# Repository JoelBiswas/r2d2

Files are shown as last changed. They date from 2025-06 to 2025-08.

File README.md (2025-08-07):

# R2-D2 - A Robotics Journey
The repository contains the files to build a smaller-scale replica of the R2-D2 droid from the Star Wars universe. The robot can move around and rotate its head, just like in the movies. It is controlled with a PS3 controller. This robotics project was created entirely by me for Hack Club's Highway to Undercity event.



FrontView

## Bill of Materials
View the Bill of Materials [here](https://docs.google.com/spreadsheets/d/11K8ikvZwUrrph38blHlkMEm7u3jJ6bzhOUvdLzmd2ws/edit?usp=sharing)

## The Start of the Journey
As a **HUGE** Star Wars fan and a robotics enthusiast, I have always thought it would be so cool to have my very own droid, just like the characters from the movies. Through my two years of experience in a FIRST Robotics Competition team (shoutout team 9477), I was able to learn all the skills I would need to build my own droid. When I was introduced to the Hack Club's Highway to Undercity event, which provides high school students with grants to build their dream projects, I knew that this would be the perfect opportunity for me to practice my robotics skills by building a droid. I decided to attempt to build R2-D2, the most iconic droid of the Star Wars Universe.

## About R2-D2
In the movies, R2 has a wide range of abilities such as movement, flight, tasers, a holographic projector, etc. For this project, I decided to focus on two key points of functionality for the droid: movement and head rotation. The robot has three "feet" -- one on the left, one on the right, and one in the center -- each containing a Pololu 12V Motor attached to a wheel. A PS3 controller is used to control the motors and move the droid. A stepper motor is used to control the rotation of R2-D2's head. An ESP32 is used in order to control all of the motor drivers.

## Overview of this Repo
**CAD** - Contains the CAD files for the robot, along with images taken in Onshape <br>
**STLs** - Contains files for each part that needs to be 3D printed <br>
**Print** - Contains the 3d print files for the Flashforge Adventurer 5M <br>
**Electrical** - Contains files from KiCAD for the robot's wiring schematics and custom symbols <br>
**Code** - Currently empty but will eventually contain the code for controlling the robot with a PS3 controller. <br>
**JOURNAL.md** - Contains an overview of exactly how I designed and built this robot <br>
**BOM.csv** - A bill of materials for the project in CSV format <br>

## Designing the Robot
Click [here](https://cad.onshape.com/documents/fbad7fda3dbb0b1c2d9d3e12/w/7637877b99adba1fcadbcc49/e/54e6ed0ce40017a6b8cdbd53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) to view the Onshape document for this project. 
The electronic design was done in KiCAD. 

CAD
Wiring

## General Steps for Assembly
1. Print all parts in the STLs folder of this repo. **IMPORTANT NOTE** Print out the BodyButtonFill.stl file six times and print Foot.stl and FootCover.stl three times.
2. Cut out a 5.8" x 6.3" sheet out of 1/8" polycarbonate.
3. Begin assembling the head by hot-gluing the blue pieces into the indents found in the dome.
4. Bolt the top part of the Lazy Susan Bearing to the bottom of the head using M4 bolts. Use the opening in the back of the head to insert the bolts.
5. Hot glue the blue body pieces into the indents found on the body.
6. Bolt the polycarbonate sheet inside the body using 4 M4 bolts.
7. Attach the stepper motor to the inside of the body, on the top face, using 4 M3 bolts.
8. Add the shaft hub to the shaft of the stepper motor.
9. Bolt the shaft hub onto the bottom of the head using 4 M4 bolts.
10. Bolt the bottom of the Lazy Susan Bearing to the top of the body using 4 M4 bolts.
11. Hot glue the blue leg pieces into the indents on the left and right legs.
12. Bolt the left and right legs into the sides of the body using 8 M4 bolts
13. Assemble each of the three feet by placing the 12V motor in the mounting area and placing the wheel on the motor. The wheel should be aligned with the cutout on the bottom of the foot.
14. Attach the left foot, right foot, and center foot to the droid using 2 M4 bolts for each foot.
15. Zip tie each electronic component (1 ESP32, 3 MD10Cs, 1 A4988, 1 12V to 5V Buck Converter, 1 3S LiPo Battery) to the polycarbonate plate using the zip tie mounts
16. Use the wiring schematic in the Electrical folder of this repo to wire the electrical components
17. Attach all the covers using M4 bolts

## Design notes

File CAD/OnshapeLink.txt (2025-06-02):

https://cad.onshape.com/documents/fbad7fda3dbb0b1c2d9d3e12/w/7637877b99adba1fcadbcc49/e/54e6ed0ce40017a6b8cdbd53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

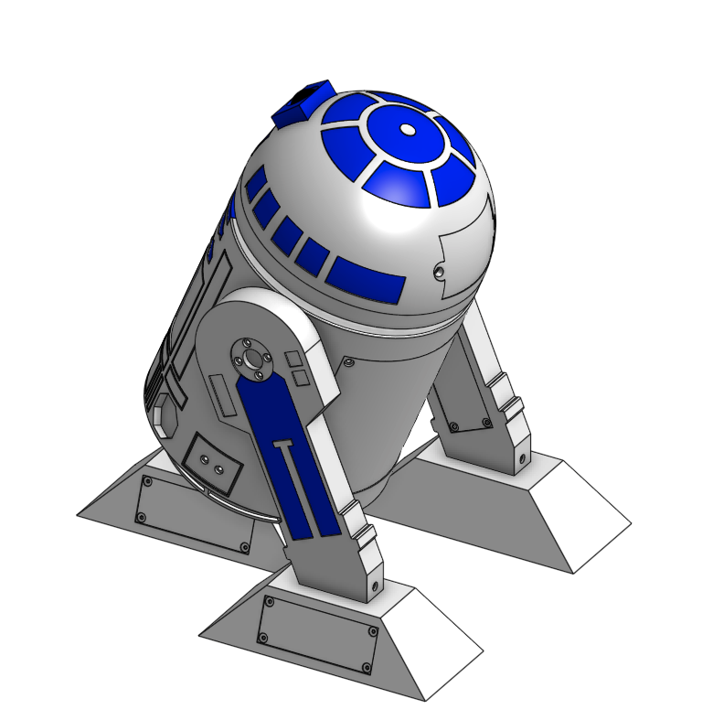
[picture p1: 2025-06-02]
CAD/Images/BackRightIsometric.png

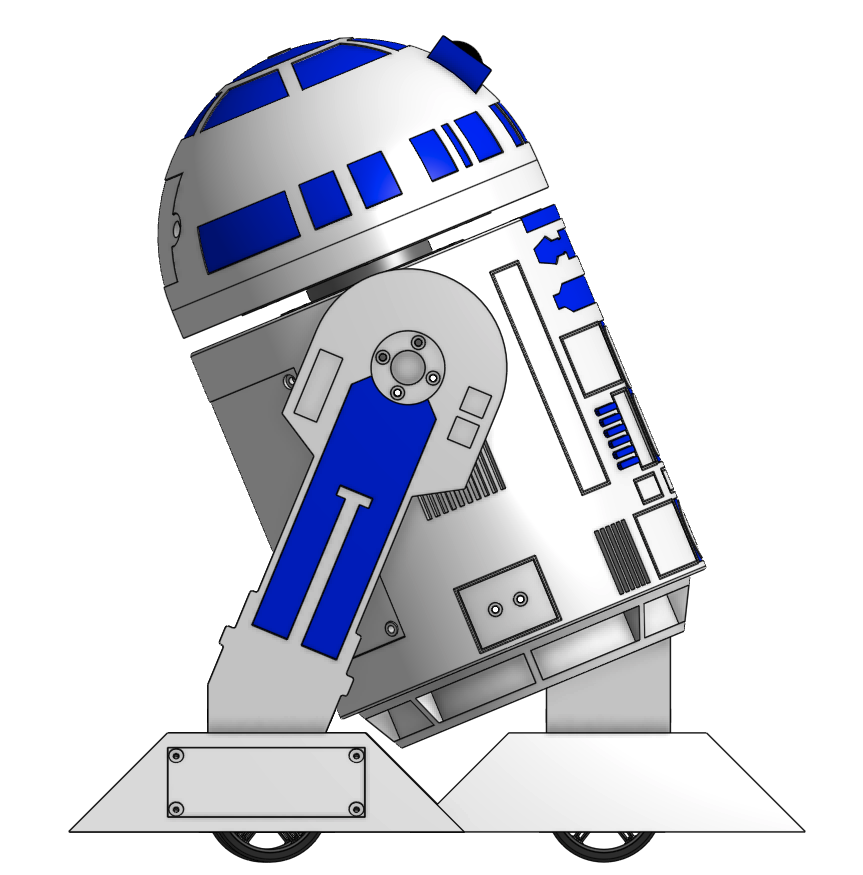
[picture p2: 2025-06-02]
CAD/Images/LeftView.png

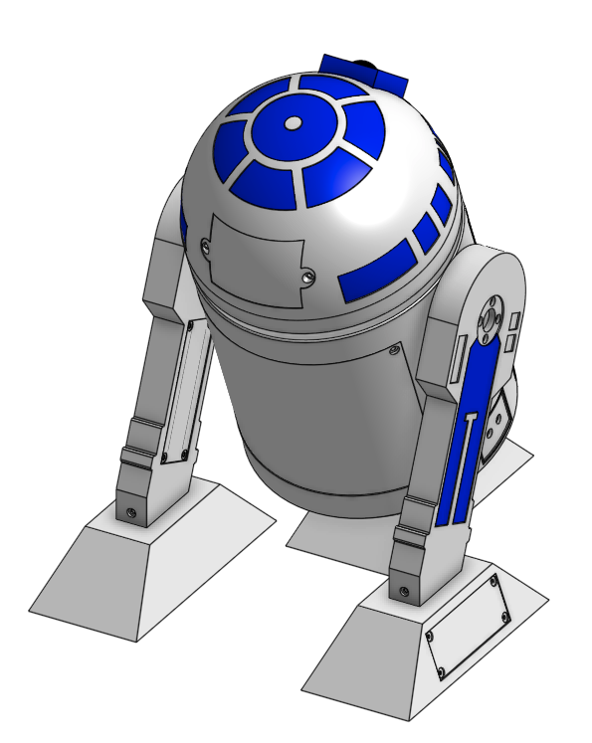
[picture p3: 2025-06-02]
CAD/Images/BackLeftIsometric.png

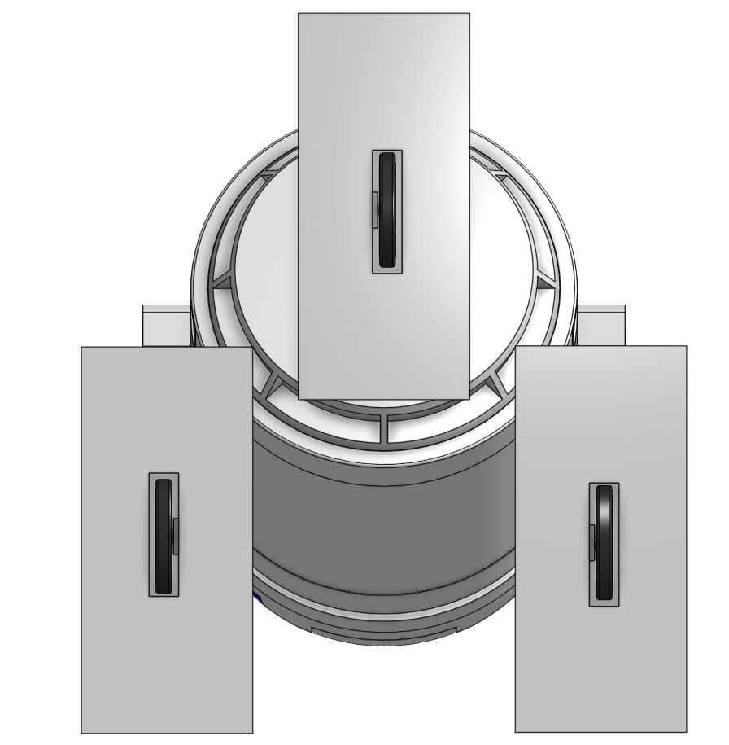
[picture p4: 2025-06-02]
CAD/Images/BottomView.png

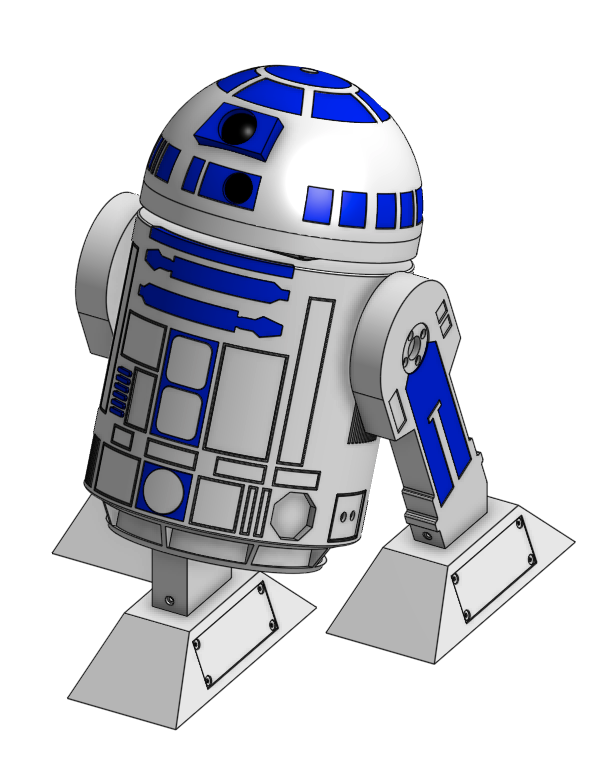
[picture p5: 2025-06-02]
CAD/Images/FrontRightIsometric.png

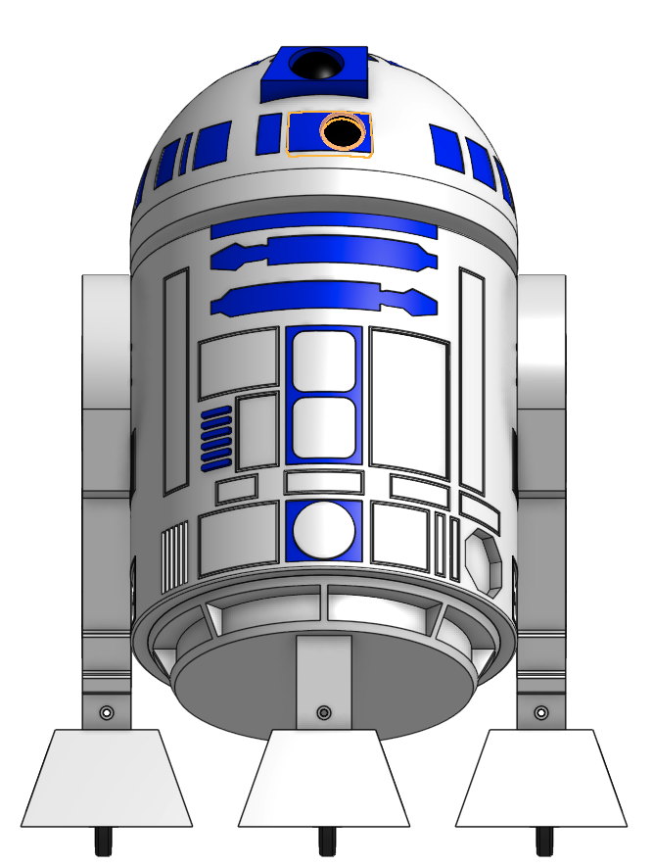
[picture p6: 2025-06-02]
CAD/Images/FrontView.png

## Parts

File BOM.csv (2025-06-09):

Part | Type | Quantity | Unit Price | Price | Link
Stepper Motor | Electrical Component | 1 | $14.00 | $14.00 | https://www.adafruit.com/product/324?gQT=1
Stepper Driver | Electrical Component | 1 | $9.95 | $9.95 | https://www.aliexpress.us/item/3256805909921734.html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:
DC Motor | Electrical Component | 3 | $22.45 | $67.35 | https://www.robotshop.com/products/12v-pololu-1501-micro-metal-gearmotor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
DC Motor Driver | Electrical Component | 3 | $13.90 | $41.70 | https://www.cytron.io/p-10amp-5v-30v-dc-motor-driver
ESP32 | Electrical Component | 1 | $4.31 | $4.31 | https://www.aliexpress.us/item/3256805517875317.html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:
3S LiPo Battery | Electrical Component | 1 | $12.89 | $12.89 | https://www.aliexpress.us/item/3256807696422912.html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:
LiPo Battery Charger | Electrical Component | 1 | $5.28 | $5.28 | https://www.aliexpress.us/item/3256807365682967.html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:
12V to 5V Buck Convertor | Electrical Component | 1 | $7.42 | $7.42 | https://www.aliexpress.us/item/3256808570929306.html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:
PS3 Controller | Electrical Component | 1 | $5.75 | $5.75 | https://www.aliexpress.us/item/2251832610701516.html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:
16 AWG Wire (Red + Black) (5m) | Electrical Component | 1 | $5.90 | $5.90 | https://www.aliexpress.us/item/3256807170658268.html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:
22 AWG WIre (Red + Black) (5m) | Electrical Component | 1 | $2.17 | $2.17 | https://www.aliexpress.us/item/3256807170658268.html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:
22 AWG Wire (White) (5m) | Electrical Component | 1 | $2.12 | $2.12 | https://www.aliexpress.us/item/3256801683674437.html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:
Wire Stripper | Electrical Component | 1 | $6.33 | $6.33 | https://www.aliexpress.us/item/3256807349448352.html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:
Electrical Tape | Electrical Component | 1 | $1.13 | $1.13 | https://www.aliexpress.us/item/3256805041931203.html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:
M4 Threaded Inserts (50 pack) | Fastener | 1 | $9.32 | $9.32 | https://www.mcmaster.com/94459A150
M3 Bolts (16mm) | Fastener | 1 | $2.05 | $2.05 | https://www.aliexpress.us/item/2251832255868282.html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:
M4 Bolts (50mm) | Fastener | 1 | $2.25 | $2.25 | https://www.aliexpress.us/item/2251832255868282.html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:
M4 Bolts (25mm) | Fastener | 2 | $1.49 | $2.98 | https://www.aliexpress.us/item/2251832255868282.html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:
Zip Ties (100 pack) | Fastener | 1 | $1.55 | $1.55 | https://www.aliexpress.us/item/3256805935303543.html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:
Zip Tie Mounts (50 pack) | Fastener | 1 | $1.69 | $1.69 | https://www.aliexpress.us/item/2255800615815847.html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:
Wheel (2-Pack) | Other | 2 | $8.75 | $17.50 | https://www.pololu.com/product/1430
Lazy Susan Bearing | Other | 1 | $6.99 | $6.99 | https://www.woodcraft.com/products/triangle-flat-square-lazy-susan-4-5-16-t-capacity-300-lbs
Shaft Hub | Other | 1 | $3.19 | $3.19 | https://www.robocore.net/item-mecanico/acoplador-5mm
1kg PLA Filament White | Other | 3 | $11.33 | $34.00 | https://www.amazon.com/ANYCUBIC-Filament-Printing-Dimensional-Accuracy/dp/B0DZ24ZZNR?sr=8-10
1kg PLA Filament Blue | Other | 1 | $17.99 | $17.99 | https://www.amazon.com/ANYCUBIC-Filament-Printing-Dimensional-Accuracy/dp/B0CZRK4Y52?sr=8-9
1/8" Thick Polycarbonate (12x12) | Other | 1 | $4.50 | $4.50 | https://www.amazon.com/LEXAN-POLYCARBONATE-CLEAR-THICK-PICK/dp/B074NB3XD1?gQT=0
Soldering Iron | Already Owned | 0 | $0.00 | $0.00
Solder | Already Owned | 0 | $0.00 | $0.00
Wire Cutters | Already Owned | 0 | $0.00 | $0.00
3D Printer | Already Owned | 0 | $0.00 | $0.00
Shipping + Tax Estimate | Other | 1 | $50.00 | $50.00
Total Price | $340.31

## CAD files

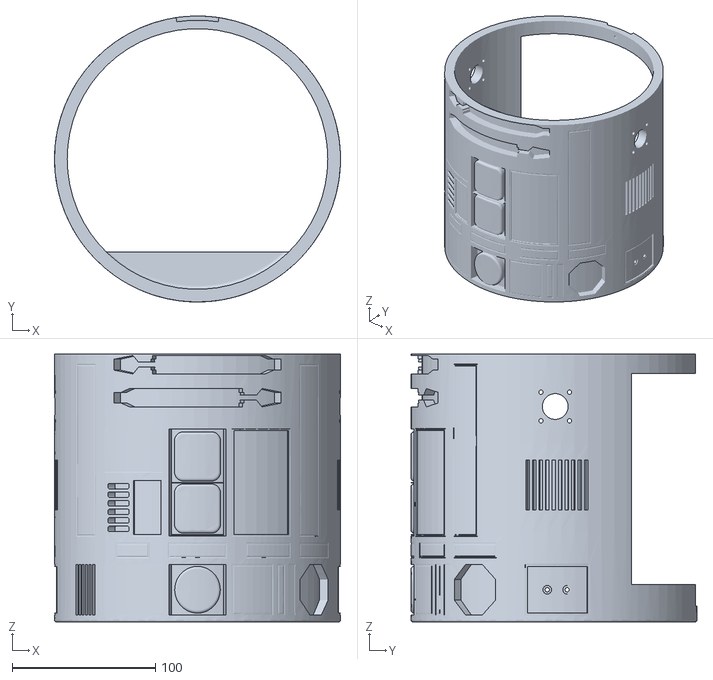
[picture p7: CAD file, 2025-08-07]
STLs/White/Body/BodyMain.stl
200.0 x 200.0 x 187.3

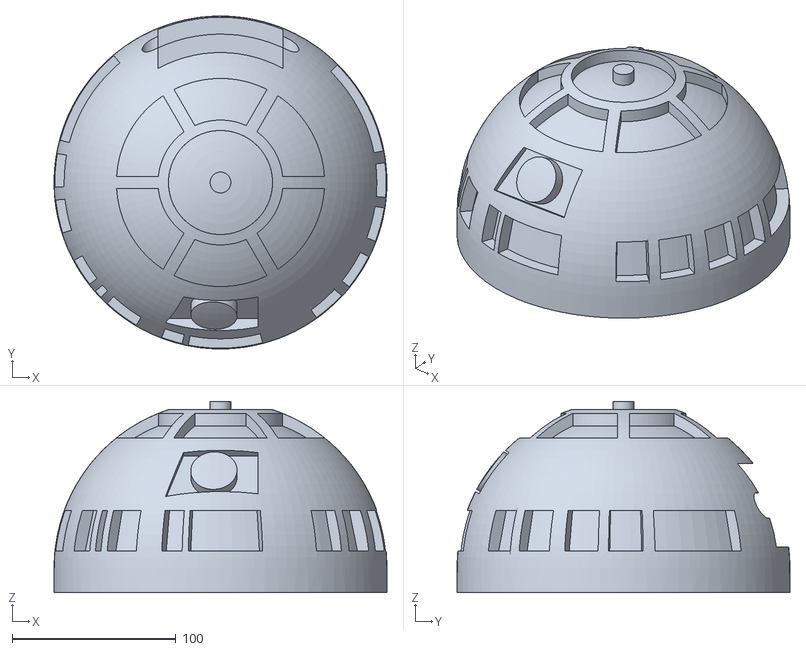
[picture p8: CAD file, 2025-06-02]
STLs/White/Head/HeadMain.stl
203.2 x 203.2 x 116.8

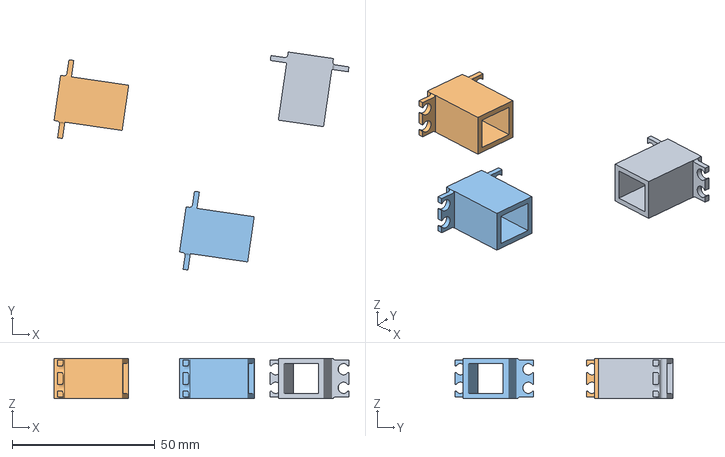
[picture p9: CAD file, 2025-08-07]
Print/Slicer/N20Case.3mf
103.2 x 76.3 x 14.0 mm
N20Case.stl x 3

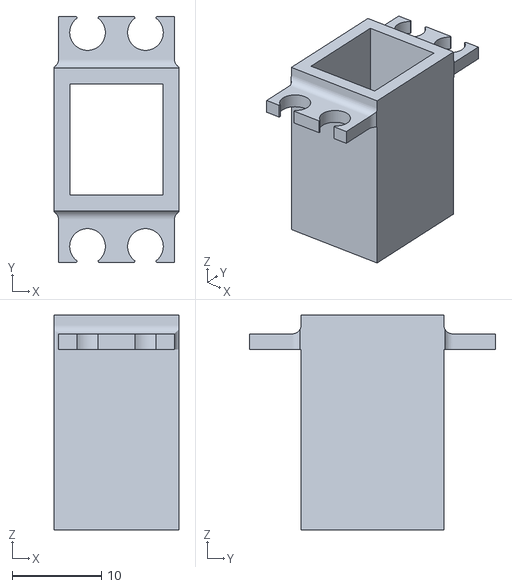
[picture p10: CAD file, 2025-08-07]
STLs/Black/Foot/N20Case.stl
14.0 x 27.6 x 24.1

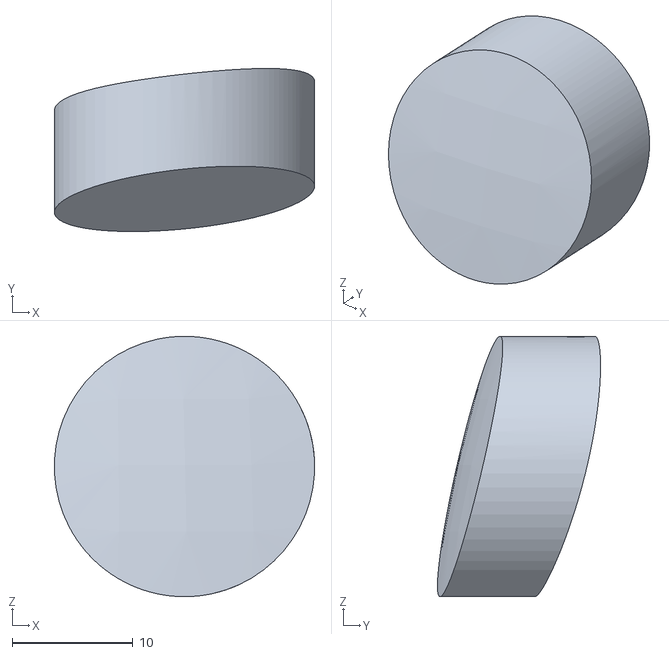
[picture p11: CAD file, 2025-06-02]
STLs/Black/Head/HeadStatusLight.stl
21.5 x 13.5 x 21.6

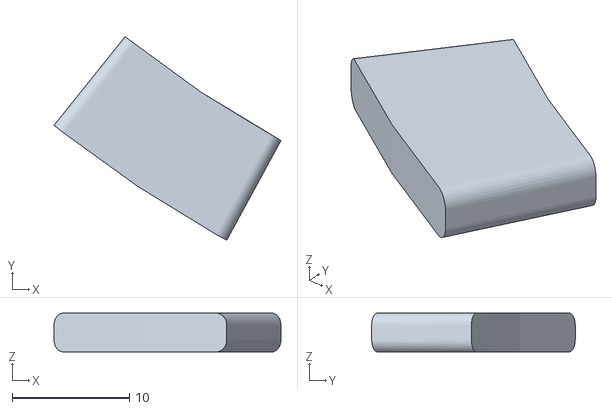
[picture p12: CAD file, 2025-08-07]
STLs/Blue/Body/BodyButtonFill2.stl
19.3 x 17.3 x 3.32

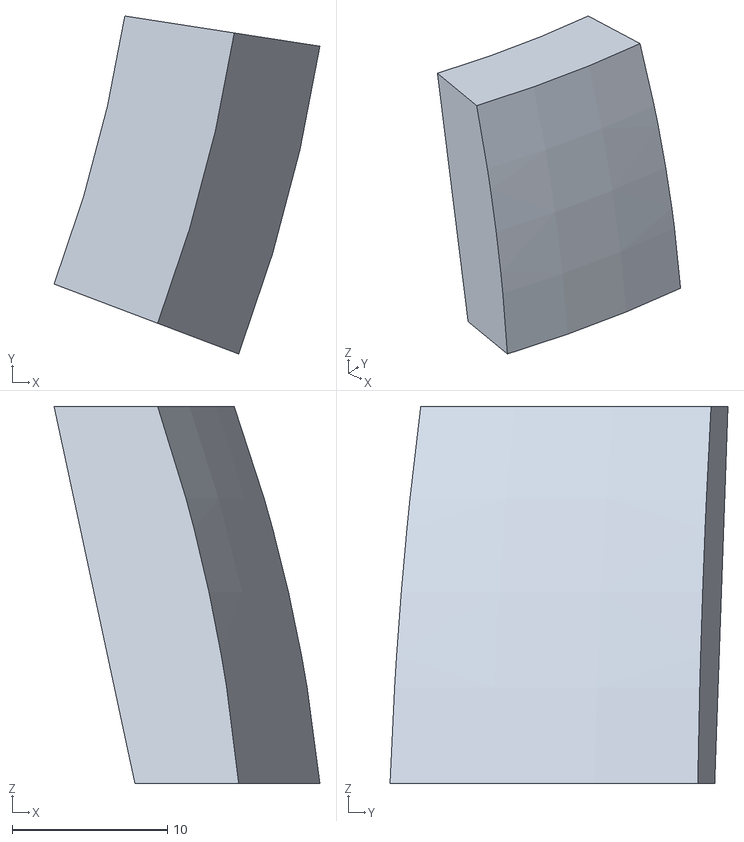
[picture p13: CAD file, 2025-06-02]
STLs/Blue/Head/HeadRightFill1.stl
17.1 x 21.7 x 24.2

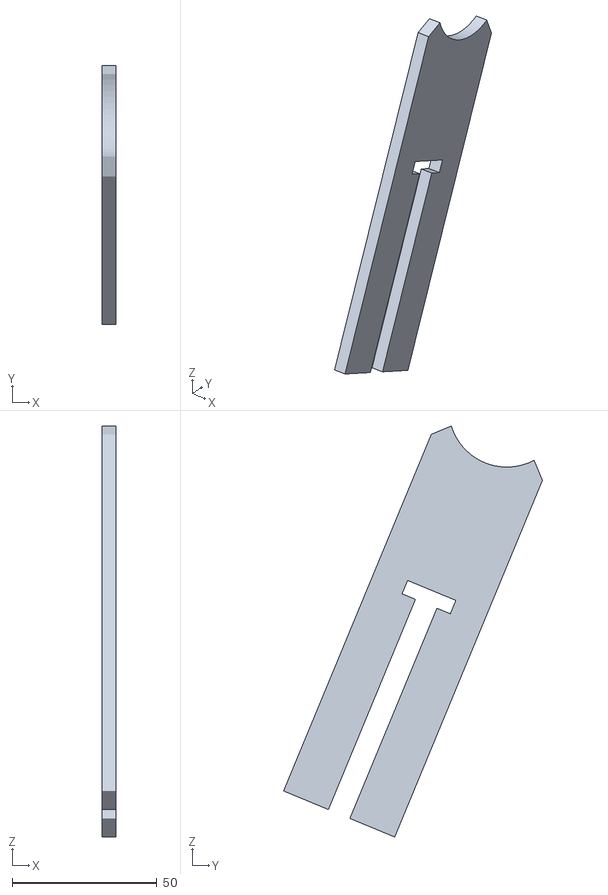
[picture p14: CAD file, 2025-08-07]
STLs/Blue/Leg/RightLegFill.stl
5.00 x 89.3 x 141.8

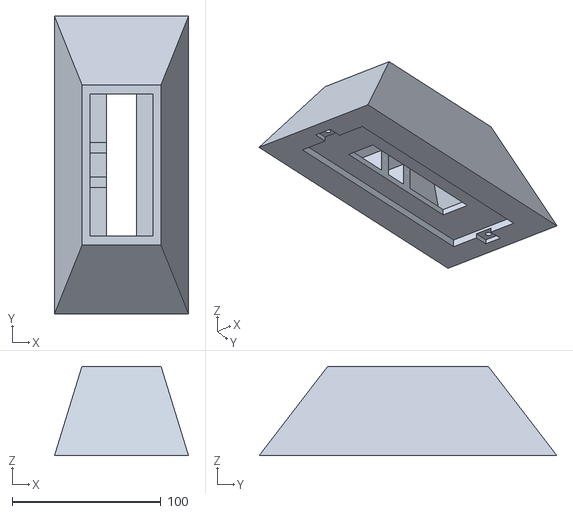
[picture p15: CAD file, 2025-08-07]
STLs/White/Foot/FootBottom.stl
90.0 x 200.0 x 60.0

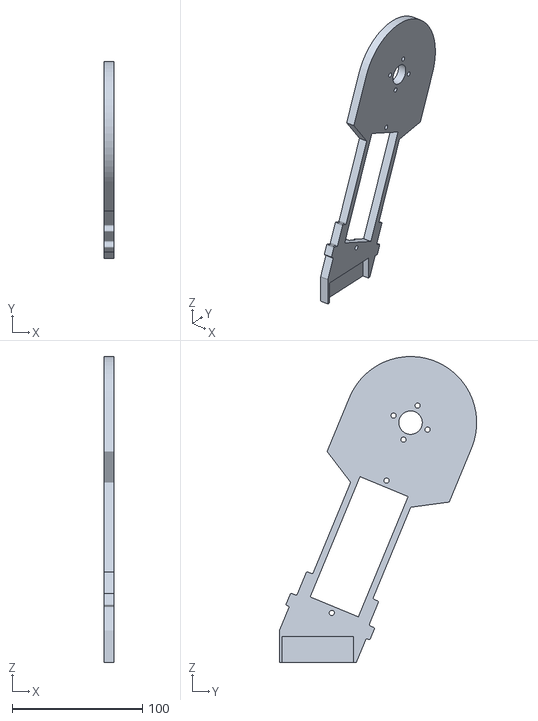
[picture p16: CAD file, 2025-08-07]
STLs/White/Leg/RightLegBottom.stl
8.00 x 151.6 x 235.1

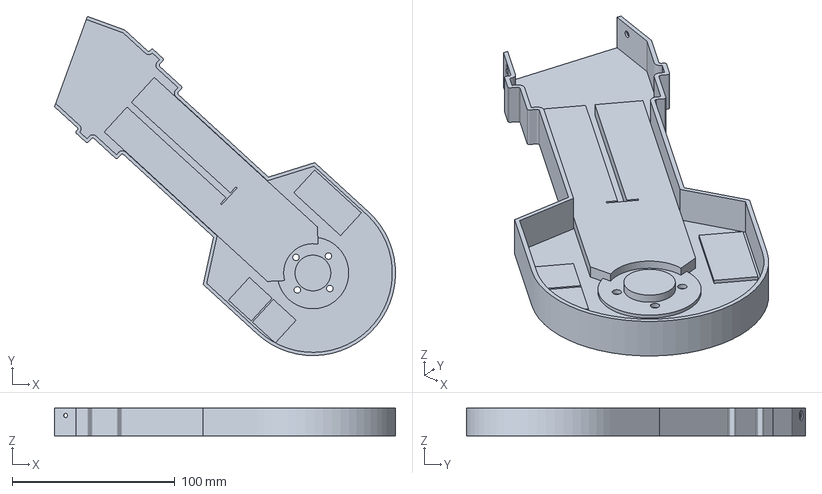
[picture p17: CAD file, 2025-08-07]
Print/Slicer/LeftLegTop.3mf
209.7 x 208.6 x 17.0 mm

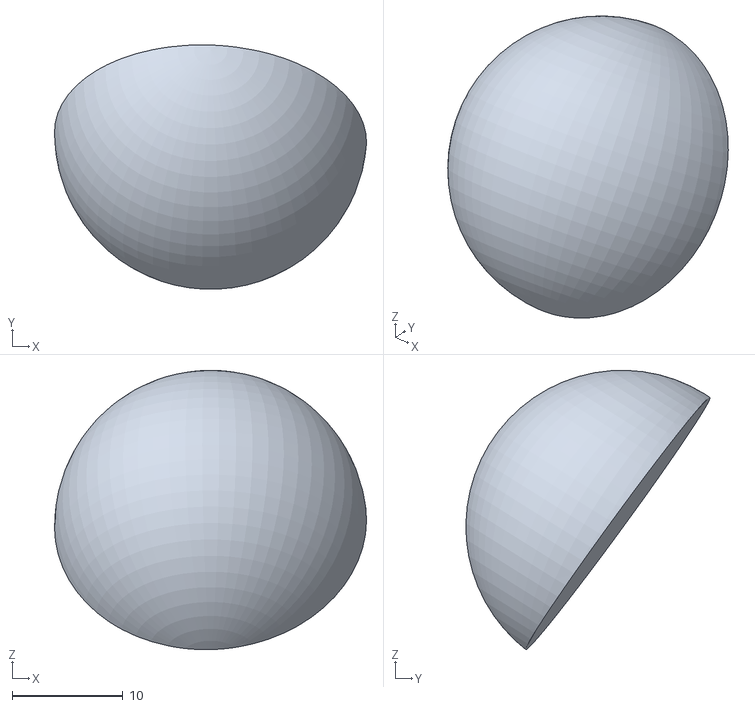
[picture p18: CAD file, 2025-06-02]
STLs/Black/Head/HeadEye.stl
28.2 x 22.1 x 25.2

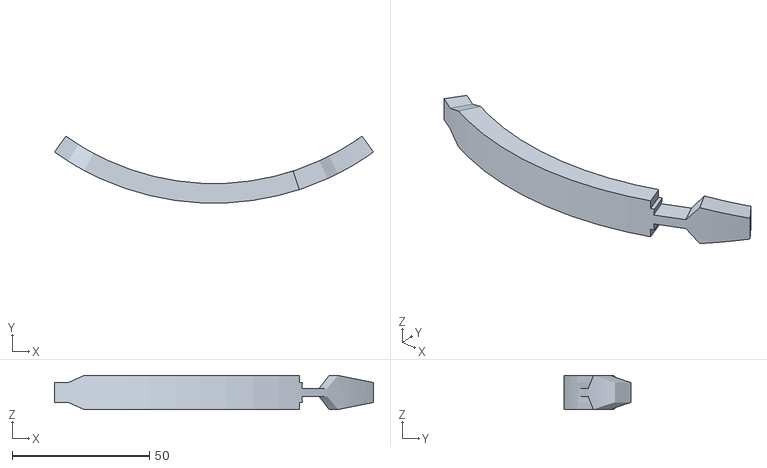
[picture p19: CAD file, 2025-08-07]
STLs/Blue/Body/BodyArmFillBottom.stl
116.1 x 24.3 x 12.4

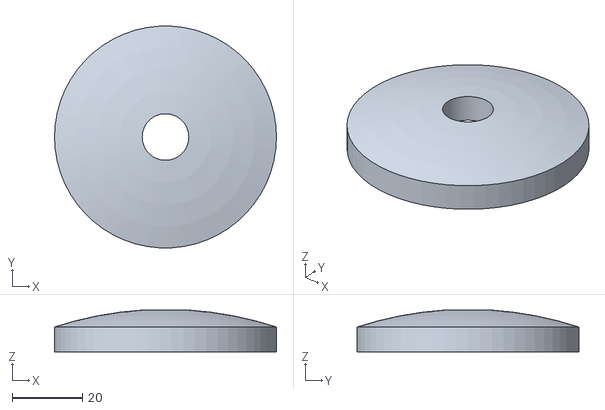
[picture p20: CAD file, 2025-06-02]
STLs/Blue/Head/HeadTopCenterFill.stl
63.0 x 62.9 x 11.9

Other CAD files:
Print/Slicer/BodyMain.3mf
Print/GCode/BodyMain.gcode.3mf
Print/GCode/BodyBottom.gcode.3mf
Print/GCode/RightLegBottom.gcode.3mf
Print/GCode/Body Top.gcode.3mf
Print/GCode/Foot.gcode.3mf
Print/GCode/FootTop.gcode.3mf
Print/GCode/LeftLegBottom.gcode.3mf
Print/GCode/LeftLegTop.gcode.3mf
Print/GCode/N20Case.gcode.3mf
Print/GCode/RightLegTop.gcode.3mf
Print/GCode/TwoFootBottom.gcode.3mf
Print/Slicer/Body Top.3mf
Print/Slicer/BodyBottom.3mf
Print/Slicer/Foot.3mf
Print/Slicer/FootTop.3mf
Print/Slicer/LeftLegBottom.3mf
Print/Slicer/RightLegBottom.3mf
Print/Slicer/RightLegTop.3mf
Print/Slicer/TwoFootBottom.3mf
STLs/Blue/Body/BodyArmFillTop.stl
STLs/Blue/Body/BodyBottomFill.stl
STLs/Blue/Body/BodyButtonFill1.stl
STLs/Blue/Body/BodyButtonFill3.stl
STLs/Blue/Body/BodyButtonFill4.stl
STLs/Blue/Body/BodyButtonFill5.stl
STLs/Blue/Body/BodyButtonFill6.stl
STLs/Blue/Body/BodyCenterFill.stl
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

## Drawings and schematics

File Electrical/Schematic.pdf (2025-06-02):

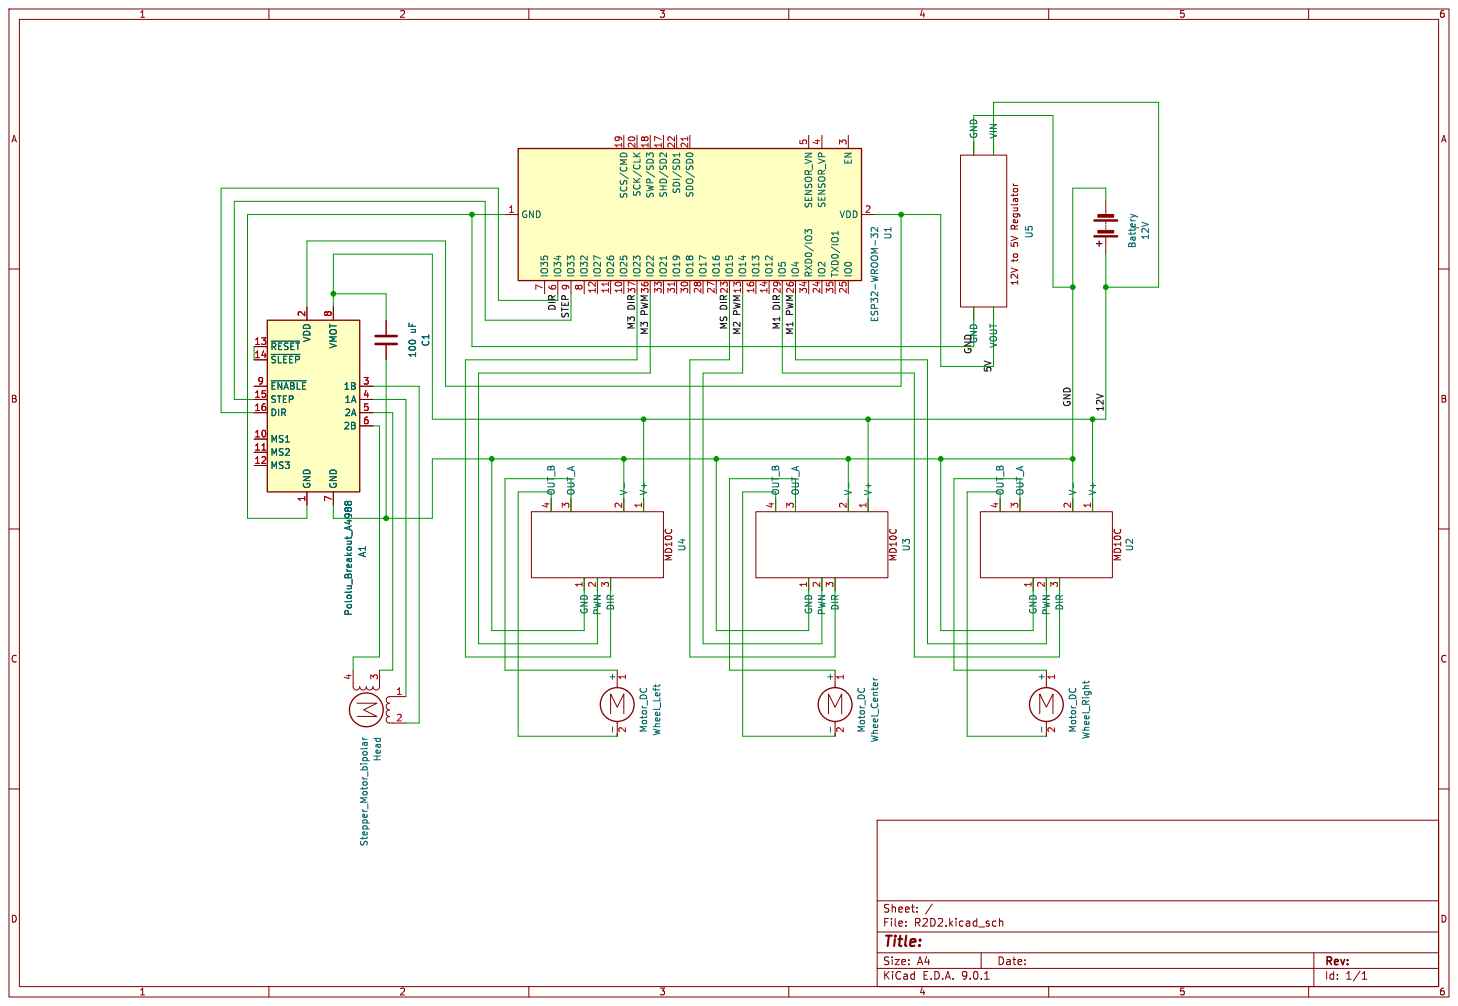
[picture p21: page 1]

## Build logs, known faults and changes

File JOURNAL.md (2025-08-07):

---
title: "R2-D2"
author: "Joel Biswas"
description: "3D Printable R2D2 droid controlled with a PS3 controller"
created_at: "2025-05-25"
---

**Total Time Spent:** 67 hours

**NOTE - As I was designing the robot, I was not very consistent with journaling. Thus, many of these entries are being written retroactively after the design has already been completed. Luckily, Onshape has a very good built-in version control system, meaning it is very easy for me to see what I did each day and how long I spent working.**

### DAY ONE - MAY 25, 2025
Today I began designing the R2D2's dome-shaped head on OnShape. The goal is for this part to be able to rotate freely. I started off by creating a Notion workspace to organize a few reference images that I would be using. My original plan was to make a life-sized R2D2, but I quickly realized that building a 3' 7" robot as my first individual hardware project would be too large of a scope. I ended up creating my own dimensions that may not be perfectly accurate to the movies, but still very closely resemble R2. The idea with the head is to separately 3D print the main dome and the blue fills. The fills can then be hot-glued into inserts on the dome. Designing this took me a fairly long time, as I have limited Onshape experience.

Day One Dome
Day One Sketch

**Time Spent:** 7 hours (over two sessions)

### DAY TWO - May 26, 2025
I began the day by finishing adding the blue sections to R2-D2's head. I then began to work on designing the body in Onshape. The body is a hollowed-out cylinder with numerous indents on the front. I once again used reference images from a Notion workspace to try to create an accurate depiction of R2-D2. Creating the designs on the body was much easier than the head, as I was able to use OnShape's wrap tool.

Day Two Dome
Day Two Body

**Time Spent:** 8 hours (over three sessions)

### DAY THREE - May 27, 2025
Today, I decided to finish adding details and indents to the front of the droid's cylindrical body. I also added a small hole to the top of the body and the bottom of the head for the axle of a stepper motor. At this point, I still do not have a very good idea of how to make the head rotate, but I intend to make a full parts list tomorrow in order to figure out the mechanism. I also used Onshape's move face tool to add clearance to the blue parts of the head and body. This allows the parts to fit together more easily when being 3D printed.

Day Three Body

**Time Spent:** 3 hours (one session)

### DAY FOUR - May 28, 2025
I began by creating a parts list on a Google Sheet in order to better organize this project. The first problem I had to figure out was how I would rotate the head separately from the body. I decided that I would mount a Stepper Motor on the inside of the body so that its axle was pointing upward towards the head. The axle of the motor would then have a shaft hub attached to it.  I would also attach a Lazy Susan Bearing to the top of the body. The head would then be attached to the Lazy Susan Bearing and the shaft hub. Thus, the motor would spin the shaft hub, which would then spin the head and the bearing. I recorded the parts that I would need for this mechanism and began designing them. I was then able to put together the head and the body in the OnShape assembly. I then began to design the legs for the side of the droid. These legs are connected through four bolt holes on each side of the body. Finally, I realized that I needed some way to insert bolts and components inside the head and the body, so I created openings in the backs of these parts. I added a 3D printable cover that can be bolted on to cover the openings

Day Four Front
Day Four Foot
Day Four Back

**Time Spent:** 8 hours (over two sessions)

### DAY FIVE - May 29, 2025
Today, I designed the droid's feet. The robot has three identical feet on the left, right, and center. I used the loft feature in OnShape to create a shape that resembles R2-D2's foot from the movies. I also found a small motor from Pololu with enough torque to be able to spin a wheel inside the foot. I added three of these motors and wheels to the parts list. I was able to find the STEP files for these parts online, so I was able to import them into my OnShape document. I added a small cutout to the bottom of the foot so that the wheel would be able to get some traction with the ground. I also added a bottom section to the droid's body that can be bolted on. This bottom section connects to the robot's center foot. Finally, after talking to a friend with much more experience with Onshape than I, I realized that the way I created the head originally was extremely inefficient. I decided to redesign the head using a much better and cleaner looking method.

Day Five Foot
Day Five Foot Without Cover
Day Five Wheel

**Time Spent:** 10 hours (over two sessions)

### DAY SIX - May 30, 2025
Today, I decided to fix one problem in the CAD from yesterday. I was using the same part for both the left leg and the right leg, when in reality, they are not the same. The right and left legs are mirrored versions of each other. I created a second part for the right leg and added it to my main assembly. After this, I was essentially done with the CAD for this project!

Day Six Left Leg
Day Six Right Leg

**Time Spent:** 2 hours (over two sessions)

### DAY SEVEN - May 31, 2025
Now that the CAD has been mostly completed, I decided to begin working on the electrical diagram for the robot. I decided that it would be slightly impractical to create a PCB as it would end up being fairly large. It would have to include an ESP32, 3 DC motor drivers, a buck converter, and a stepper motor driver. I decided that I would create a wiring schematic and then simply connect the components using wires rather than a PCB. I designed the schematic in KiCAD and used a custom symbol for the DC motor driver.

Day Seven Wiring

**Time Spent:** 3 hours

### DAY EIGHT - June 1, 2025
Today, I added the final pieces to the OnShape document. I decided to add a polycarbonate sheet to the inside of the robot in order to mount all of the electronics, too. Using the CAD model, I found that the sheet's dimensions should be 5.8" x 6.3". I added this panel to the CAD and then added holes so that wires can be funneled from the body to the feet. Finally, I made sure to add proper clearance to all parts so that they would fit together correctly after 3D printing.

Day Eight Back

**Time Spent:** 2 hours

### DAY NINE - June 2, 2025
Now that the initial design for the droid is done, I finally compiled all of my files into this GitHub repo. I created a folder for CAD files, a folder for electrical schematics, a folder for 3D print files, and an empty folder for code. I then began updating the README.md file to have all the information about this project.

**Time Spent:** 4 hours

### DAY TEN - July 31, 2025
**Time Spent:** 5 hours
I took a long break from this project while I waited for parts to arrive. During this time, I primarily worked on other projects. The five hours were spent slicing print files and making small adjustments to the CAD, in order to prepare for printing. As of today, I have officially received all my orders and have 3D printed all of the parts.

### Day ELEVEN - August 6, 2025
**Time Spent** 15 hours
I spent about a week assembling the robot and writing firmware. The assembly proved challenging due to this being the first multiple part project that I have worked on. Additionally, I had ordered M3 threaded inserts, despite using M4 bolts, leading to even more complications. The firmware used the left joystick to control the left wheel of the robot afn the right joystick to contrl the right wheel of the robot. The middle wheel's speed is set to the average of the other two wheels.


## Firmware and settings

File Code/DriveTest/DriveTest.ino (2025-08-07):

#include <Bluepad32.h>

constexpr uint8_t STATUS_LED = 2;
constexpr uint8_t LEFT_PWM = 12;  
constexpr uint8_t LEFT_DIR = 13;
constexpr uint8_t MID_PWM = 27;
constexpr uint8_t MID_DIR = 14;
constexpr uint8_t RIGHT_PWM = 25;
constexpr uint8_t RIGHT_DIR = 26;

ControllerPtr myControllers[BP32_MAX_GAMEPADS];

void onConnectedController(ControllerPtr ctl) {
  Serial.println("Controller connected");
  myControllers[0] = ctl;
  digitalWrite(STATUS_LED, HIGH);
  ctl->playDualRumble(0, 500, 255, 128);
}

void onDisconnectedController(ControllerPtr)   {
  Serial.println("Controller disconnected");
  myControllers[0] = nullptr;
  digitalWrite(STATUS_LED, LOW);
}

void driveMotor(uint8_t dirPin, uint8_t pwmChannel, int16_t input) {
  const int DEADZONE = 100;
  if (abs(input) < DEADZONE) {
    ledcWrite(pwmChannel, 0);
    return;
  }

  uint8_t duty = map(abs(input), DEADZONE, 512, 0, 255);

  if (input > 0)        digitalWrite(dirPin, HIGH);
  else                   digitalWrite(dirPin, LOW);

  ledcWrite(pwmChannel, duty);
}

void processGamepad(ControllerPtr ctl) {
  int16_t rightInput = -ctl->axisRY();
  int16_t leftInput = ctl->axisY();
  int16_t midInput = ((-1 * leftInput) + rightInput) / 2;
  driveMotor(RIGHT_DIR, 0, rightInput);
  driveMotor(MID_DIR, 1, midInput);
  driveMotor(LEFT_DIR, 2, leftInput);
}

void setup() {
  Serial.begin(115200);

  pinMode(LEFT_DIR, OUTPUT);
  pinMode(MID_DIR, OUTPUT);
  pinMode(RIGHT_DIR, OUTPUT);
  pinMode(STATUS_LED, OUTPUT);

  const int FREQ = 20000;
  const int BITS = 8;

  ledcSetup(0, FREQ, BITS);
  ledcSetup(1, FREQ, BITS);
  ledcSetup(2, FREQ, BITS);
  ledcAttachPin(RIGHT_PWM, 0);
  ledcAttachPin(MID_PWM, 1);
  ledcAttachPin(LEFT_PWM, 2);
  ledcWrite(0, 0);
  ledcWrite(1, 0);
  ledcWrite(2, 0);

  digitalWrite(STATUS_LED, LOW);

  BP32.setup(&onConnectedController, &onDisconnectedController);
  BP32.forgetBluetoothKeys();
  BP32.enableVirtualDevice(false);
}

void loop() {
  if (BP32.update()) {
    ControllerPtr ctl = myControllers[0];
    if (ctl && ctl->isConnected() && ctl->hasData() && ctl->isGamepad())
      processGamepad(ctl);
  }
  delay(10);                      // yield to BT stack
}

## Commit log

2025-06-02 Added BOM.csv
    [BOM.csv]
2025-06-04 Removed BOM.csv
    [BOM.csv]
2025-06-09 Added Print Files
    [BOM.csv]
2025-06-17 Edited STLs
    [BodyBottomFill.stl, BodyCenterFill.stl, LeftLeg.stl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]
2025-08-07 Added Firmware
    [Body Top.3mf, Body Top.gcode.3mf, Body Top.stl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]
